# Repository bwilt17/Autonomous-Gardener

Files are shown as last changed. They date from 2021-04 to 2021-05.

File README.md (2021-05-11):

# Autonomous Gardener V1.0

A mechatronics course project designed to autonomously care for a potted plant.

## Project Overview 

This project was designed and produced by Manraj Banghu and Beverly Wilt at San Jose State University in Spring 2021. Because of meeting constraints due to the Covid-19 pandemic, the project was done collaboratively online and two physical prototypes were made for testing, one for each team member.

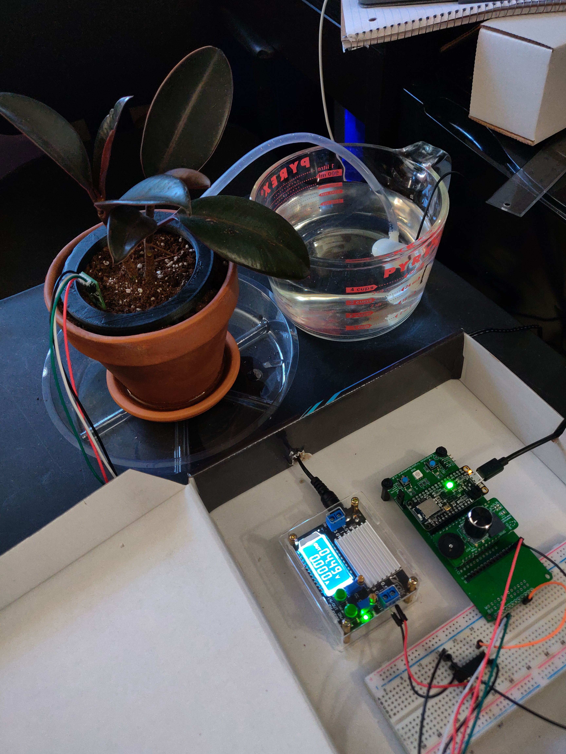
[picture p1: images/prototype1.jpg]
  

## General Design and Goals

**Goal Product:**
  - Autonomous plant caretaker that interfaces the Adafruit nRF52840 sense microcontroller with the following:
    - 3V Water Pump
    - BH1750 Light Sensor(s)
    - STEMMA I2C Capacitive Soil Moisture Sensor

***Note:** Due to shipping issues during the Covid-19 pandemic, the light sensors were ultimately replaced with the integrated temperature sensor on the STEMMA due to lack of connector components.*

**Design Goals:**
  - Not to exceed $100 budget (including university provided components)
  - Sized for reasonable desktop use
  - Makes use of 3D printed water distribution part sized for use in a basic 4.5in terracotta pot from Home Depot and saucer
  - No heavier than 5lbs 

***(UPDATE: 5/10/21)** The final prototype accomplished all of the design goals EXCEPT the weight restriction due to the weight of the water reservoir and moistened soil. Final specifications to be added at a later date.*

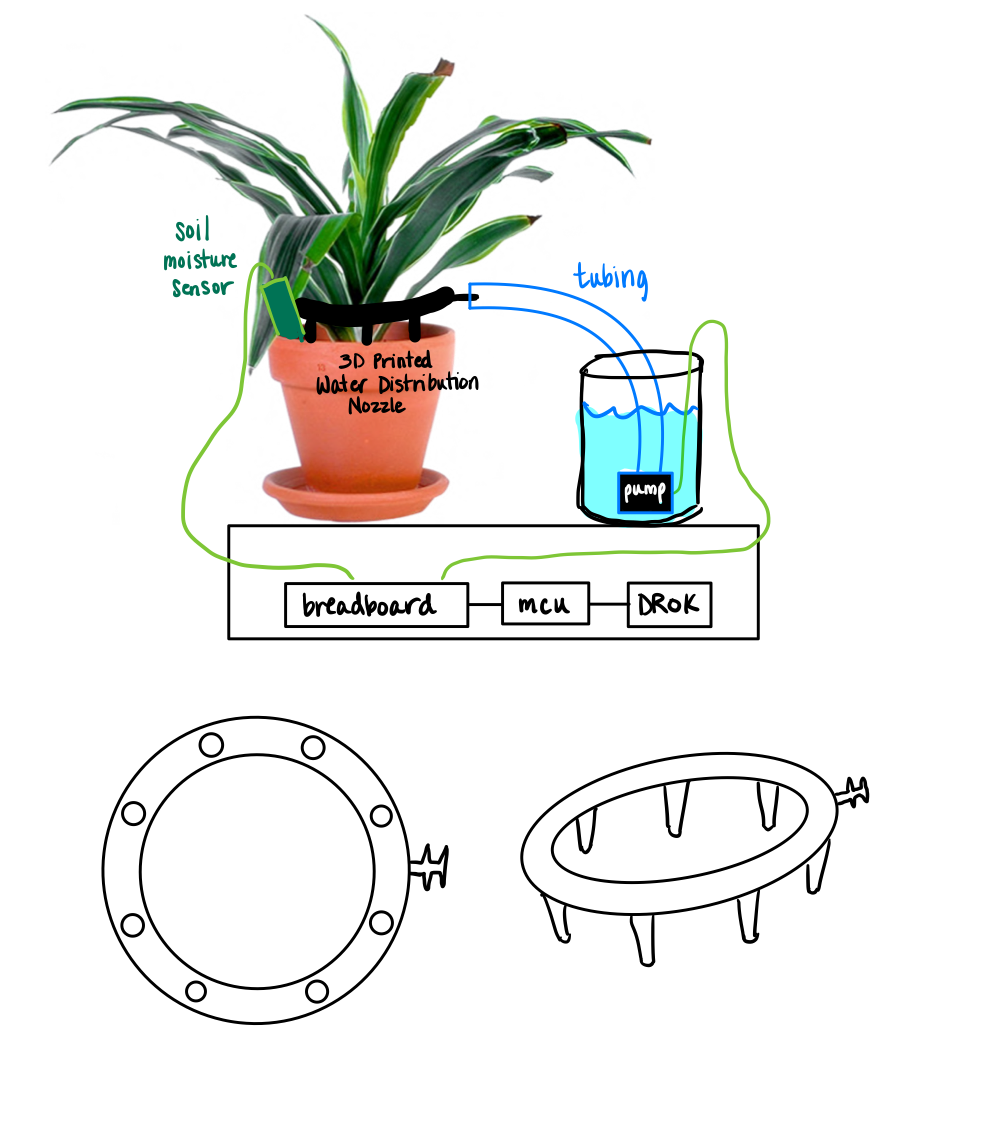
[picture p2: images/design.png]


## Water Distribution Part Info

A part for this project to distribute water around the pot was designed in SolidWorks and 3D printed. Print specifications and 3D model files can be found under [CAD files](https://github.com/bwilt17/Autonomous-Gardener/tree/main/CAD%20files).

***(UPDATE: 4/5/21)** Part design needs to be modified to have longer stakes for better soil penetration OR soil level in final potted plant used must be specified to be no lower than approx. 1/2" from the top edge of the pot.*

***(UPDATE: 5/10/21)** For the purposes of this course project, soil level in final potted plant was specified and increased to appropriate level. Another issue found in the final prototype is that the nozzle outlets furthest from the inlet have trouble getting water, presumably because the pump does not fill the nozzle completely in its runtime. Need stronger pump to ensure complete fill and/or narrower interior section.* 

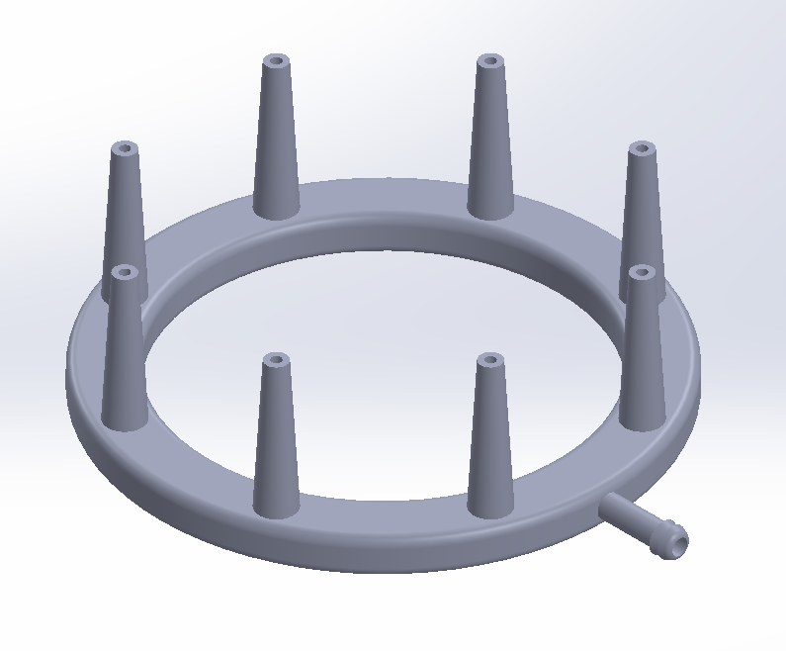
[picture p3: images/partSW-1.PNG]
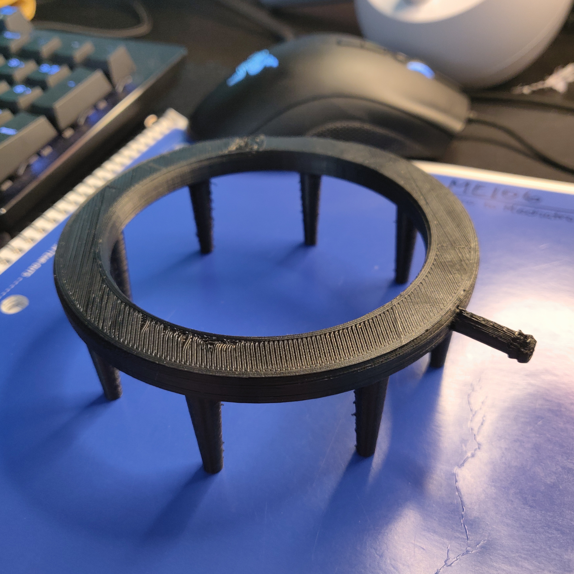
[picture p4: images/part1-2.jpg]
 

## Circuit Design:

The interface circuit makes use of a darlington transistor acting as a switch for the pump control. This simplified the circuit design, as it was similar to a setup from a course lab assignment, and allowed us to PWM for better control over pump speed. 

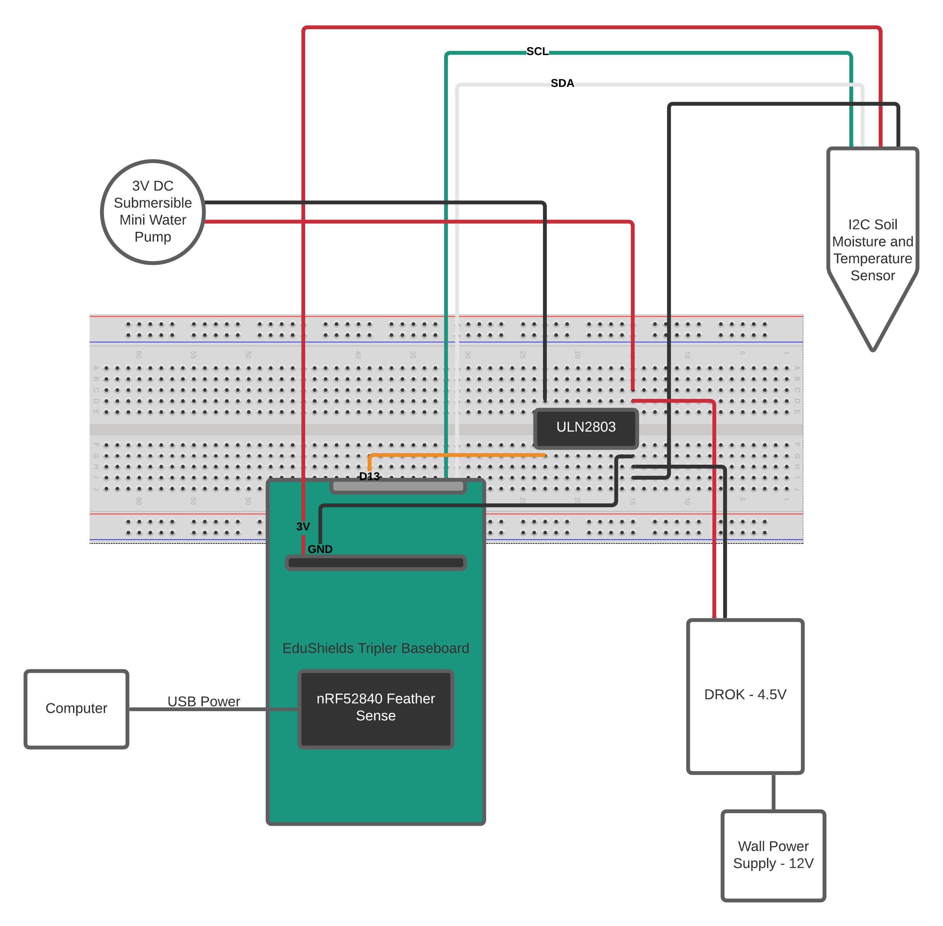
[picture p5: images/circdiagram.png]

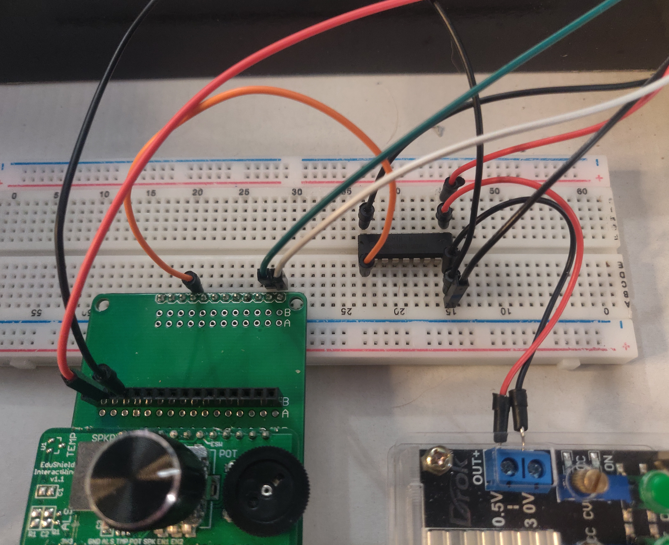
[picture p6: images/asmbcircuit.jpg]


## Coding

The program for the autonomous gardener was made in CircuitPython with Mu as a main editor and user interface. The full code, as presented for the course, can be found under [code](https://github.com/bwilt17/Autonomous-Gardener/tree/main/code).

A general flowchart for the program can be seen below:

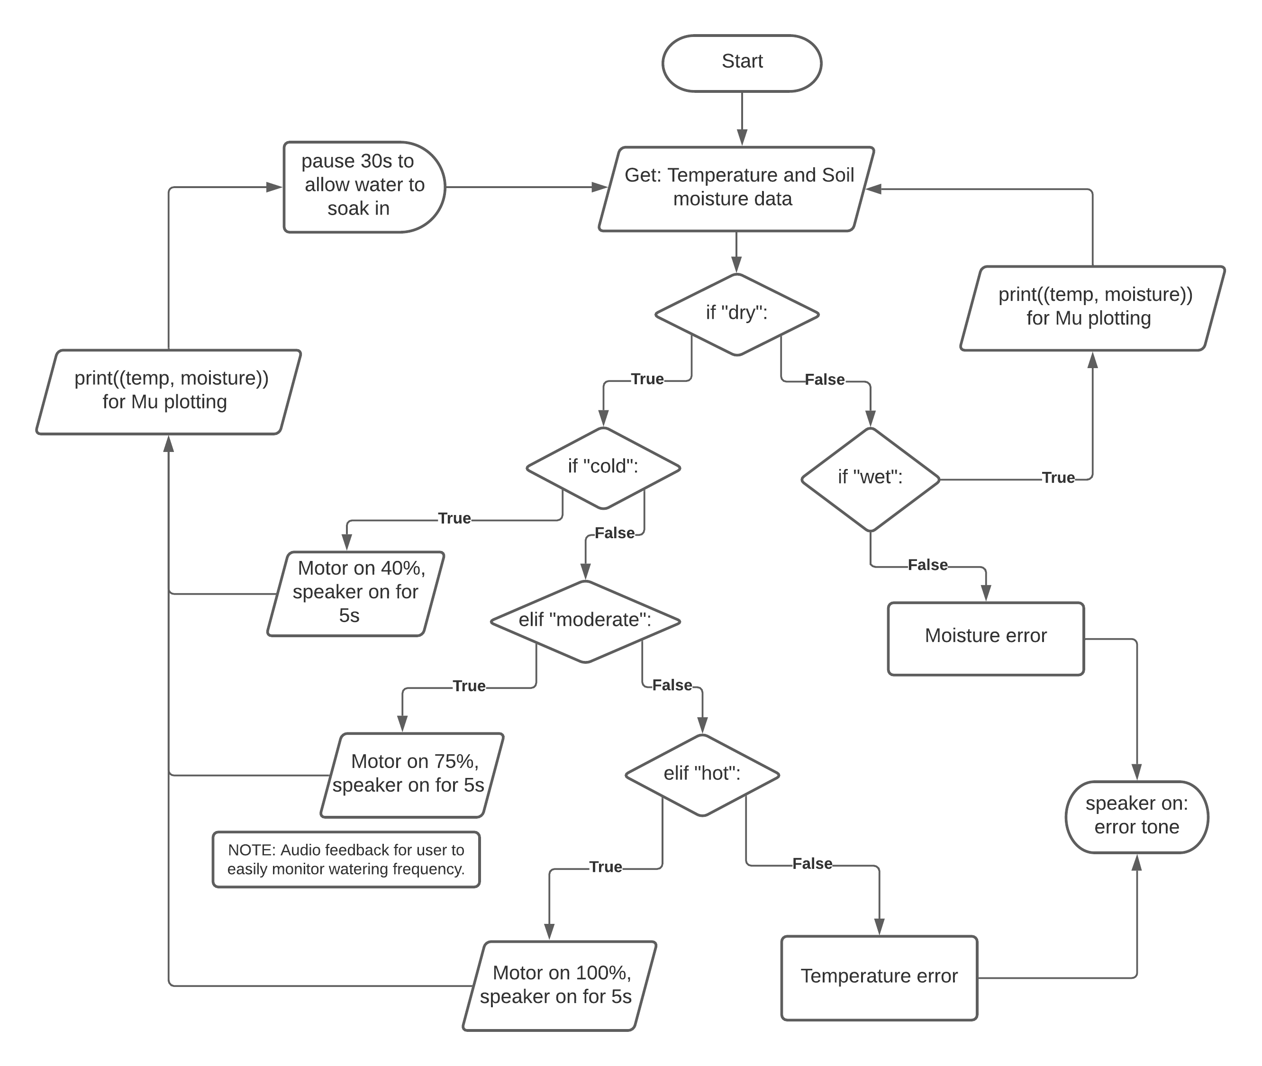
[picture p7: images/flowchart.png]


## Proof of Functionality

A short video showcasing the prototype's functionality can be found on [Youtube](https://www.youtube.com/watch?v=F2NkZJcwzsY).

## Improvements/Recommendations

The following are some suggestions for future improvement, to be done in V2.0: 
  - Decrease electronics footprint by putting nRF directly on breadboard 
     - Need external speaker OR replace moisture sensor with one that has integrated speaker to keep error/pump audio cues
  - Waterproof box to contain electronics to prevent shorting/damage
  - Add a water level sensor (ultrasonic sensor?) to the reservoir to prevent motor damage due to low water level
  - Battery/LCD screen integration to remove need for computer tether
  - Larger water reservoir for less user-dependency
  - Housing that combines electronics, reservoir, etc. into a more polished product
  - Different plant type scenarios (ie. succulent, tropical, etc.) for moisture regulation, or allow for user input

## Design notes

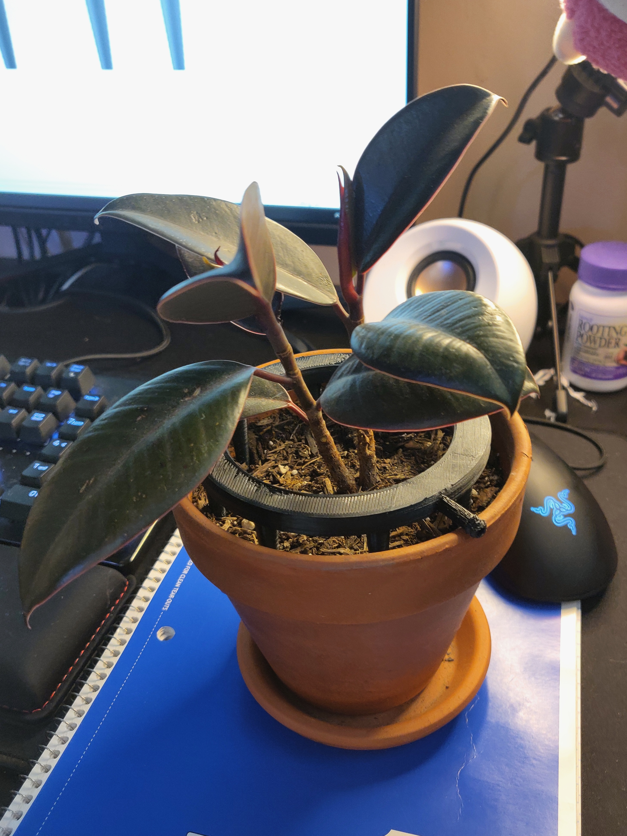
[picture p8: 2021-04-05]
images/part1-1.jpg

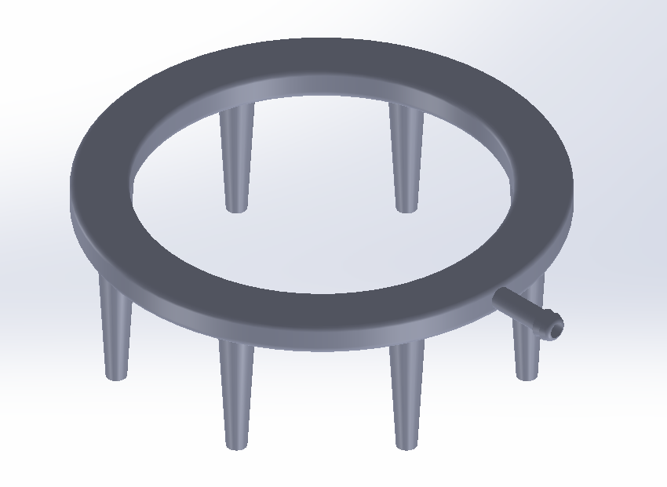
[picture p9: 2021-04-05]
images/partSW-2.PNG

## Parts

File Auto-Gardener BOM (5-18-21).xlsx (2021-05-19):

Index | Quantity | Description | Product Link (NOTE: Adafruit components also available from Digi-Key by searching product number) | Unit Price (USD) | Extended Price (USD)
1 | 1 | TUBING PVC 6MM ID X 1 METER | https://www.adafruit.com/product/4545 | $1.50 | $1.50
2 | 1 | SUBMERSIBLE 3VDC HORIZONTAL PUMP | https://www.adafruit.com/product/4546 | $1.95 | $1.95
3 | 1 | ADAFRUIT STEMMA SOIL SENSOR | https://www.adafruit.com/product/4026 | $7.50 | $7.50
4 | 3 | ADAFRUIT BH1750 LIGHT SENSOR | https://www.adafruit.com/product/4681 | $4.50 | $13.50 | NOT USED
5 | 1 | ADAFRUIT NRF52840 FEATHER SENSE WITH BASEBOARD AND INTERACT WING | Provided by SJSU, components available from Adafruit. (see below) | $40.00 | $40.00
6 |  |  | https://www.adafruit.com/product/4516
7 | 2 | STEMMA QWIIC JST SH CABLE 100MM | https://www.adafruit.com/product/4210 | $0.95 | $1.90 | NOT USED
8 | 1 | JST SH 4-PIN TO PREMIUM MALE HEADER | https://www.adafruit.com/product/4209 | $0.95 | $0.95 | NOT USED
9 | 1 | JST PH 4-PIN TO MALE HEADER CABLE | https://www.adafruit.com/product/3955 | $1.50 | $1.50
10 | 1 | FULL-SIZE SOLDERLESS BREADBOARD | https://www.adafruit.com/product/239 | $5.95 | $5.95
11 | 1 | JUMPER WIRE M TO F 6" 28AWG | https://www.adafruit.com/product/1954 | $1.95 | $1.95
12 | 1 | JUMPER WIRE M TO M 6" 28AWG | https://www.adafruit.com/product/1957 | $3.95 | $3.95
13 | 1 | PENNINGTON 4.5'' TERRA COTTA CLAY POT | https://www.homedepot.com/p/Pennington-4-5-in-Terra-Cotta-Clay-Pot-100043011/100332408 | $0.97 | $0.97
14 | 1 | PENNINGTON 4.25'' TERRA COTTA CLAY SAUCER | https://www.homedepot.com/p/Pennington-4-25-in-Terra-Cotta-Clay-Saucer-100043034/100175939 | $0.97 | $0.97
 |  | NOTE: Cost of 3D printing filament not included, considered to be negligible as it would be an unknown fraction of the price of a spool.
 |  | For reference, a 1kg spool of PLA filament is generally $20-25.
 |  |  |  | Total Cost (USD): | $66.24 | (Does not included unused components)
 |  |  |  | (not including tax/shipping)
 |  |  |  | Budget (USD): | $100.00
 |  |  |  | (not including tax/shipping)
 |  |  |  | Difference (USD): | $33.76

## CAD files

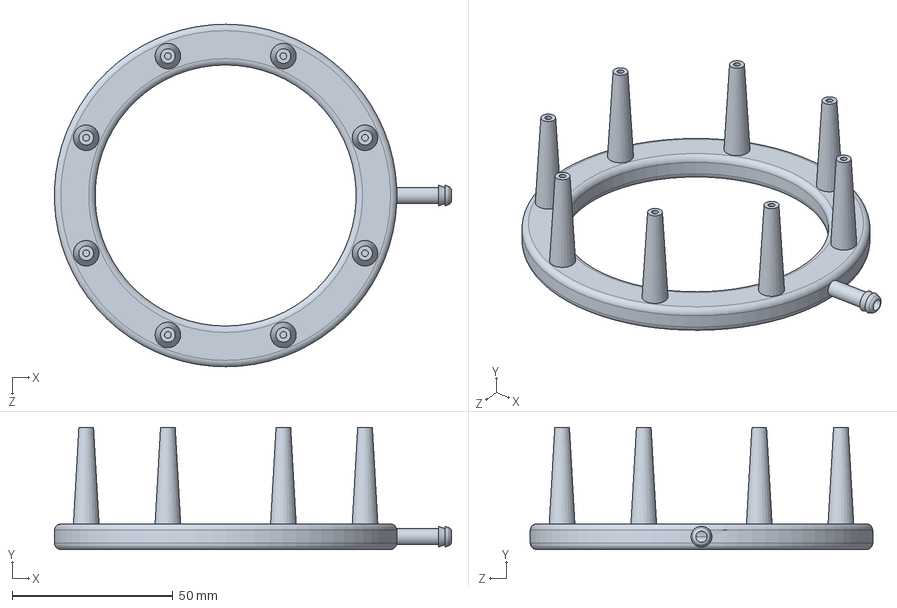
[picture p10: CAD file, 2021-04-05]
CAD files/waterpart.SLDPRT
123.6 x 38.0 x 106.7 mm

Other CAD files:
CAD files/waterpart.STL

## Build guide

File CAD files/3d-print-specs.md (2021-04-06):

# 3D Print Specifications

Printer: Kingroon KP3

Filament Type: PLA 

Filament Brand: Hatchbox

Nozzle Temp: 190 C

Bed Temp: 60 C

Printing Speed: 30 mm/s

Supports?: Yes

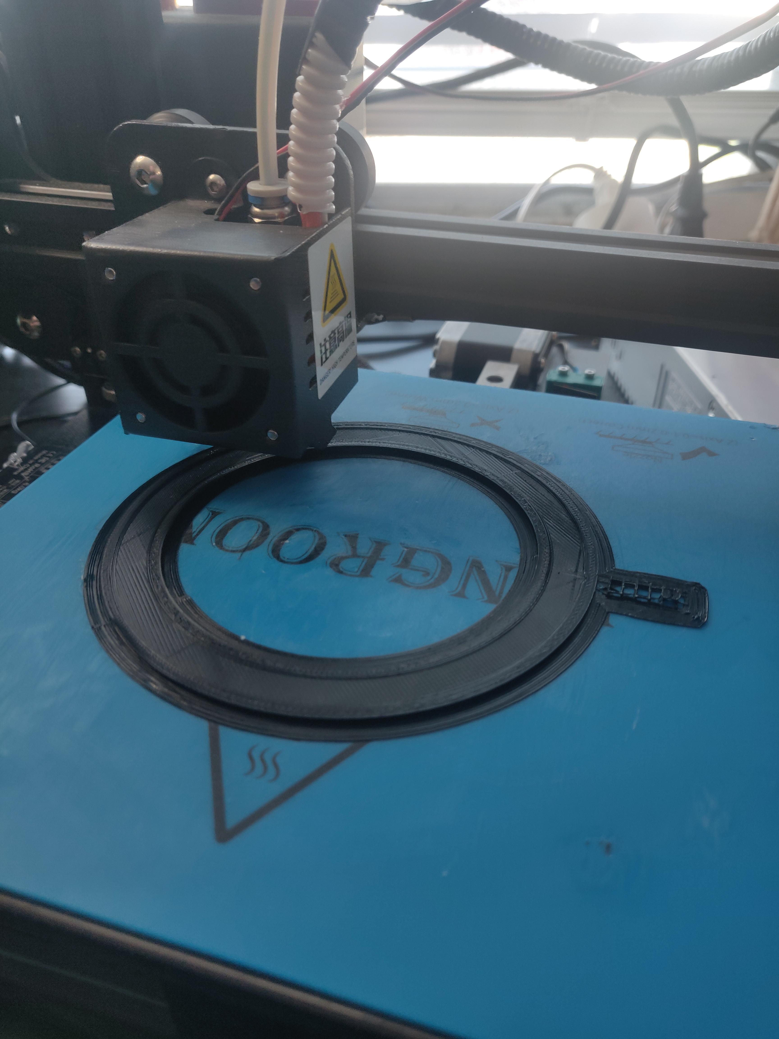
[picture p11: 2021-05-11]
images/print.jpg

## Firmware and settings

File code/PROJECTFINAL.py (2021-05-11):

import board
import pulseio
import time
from board import SCL, SDA
import busio
from adafruit_seesaw.seesaw import Seesaw

motor = pulseio.PWMOut(board.D13)
i2c_bus = busio.I2C(SCL, SDA)
ss = Seesaw(i2c_bus, addr=0x36)
spkr_pwm = pulseio.PWMOut(board.A3, variable_frequency=True)

frequency = 659

lastTime = time.monotonic()

def pwm_level(pin, inc):
    pin.duty_cycle = int((0.1 * inc) * ((2 ** 16) - 1) - 0.1)

def play(freq):
    spkr_pwm.frequency = freq
    spkr_pwm.duty_cycle = 2 ** 15

def stop():
    spkr_pwm.duty_cycle = 0

def error_beep():
    while True:
        play(650)
        time.sleep(1)
        play(450)
        time.sleep(1)
        play(250)

def readingsensor(SoilVal, TempVal, last_time):
    if SoilVal <= 400:  # Get data from soil sensor dry
        if TempVal <= 0:
            print("Weather is too cold! Bring plant to warmer area.")
            error_beep()
        elif 0 < TempVal <= 13:  # cold data from temp
            print("The plant is dry and the temperature is cold.")
            print("-> Pump on")
            play(frequency)  # Play speaker
            motor.duty_cycle = int(0.4*(2**16-1))
            time.sleep(5)
            motor.duty_cycle = 0
            stop()
        elif 13 < TempVal <= 28:  # moderate data from temp
            print("The plant is dry and the temperature is moderate.")
            print("-> Pump on")
            play(frequency)  # Play speaker
            motor.duty_cycle = int(0.75*(2**16-1))
            time.sleep(5)
            motor.duty_cycle = 0
            stop()
        elif 28 < TempVal <= 36:  # hot data from temp
            print("The plant is dry and the temperature is hot.")
            print("-> Pump on")
            play(frequency)  # Play speaker
            motor.duty_cycle = (2**16-1)
            time.sleep(5)
            motor.duty_cycle = 0
            stop()
        elif 36 < TempVal:  # extreme data from temp
            print("Weather is too hot! Bring plant to cooler area.")
            error_beep()
        else:
            print("Temperature error. Please check sensor.")
            error_beep()
    elif 400 < SoilVal <= 1000:  # Get data from soil sensor (wet)
        print("Soil is already moist and does not need to be watered.")
    elif SoilVal > 1000:
        print("Overwatered! Please check plant.")
        error_beep()
    else:
        print("Soil Moisture error. Please check sensor.")
        error_beep()

def plot(s,t):        # Plot the data print((moisture, temp))
    print((s, t))
    time.sleep(0.5)

while True:
    # Read sensor
    SoilVal = ss.moisture_read()
    TempVal = ss.get_temp()
    plot(SoilVal, TempVal)
    if time.monotonic()-lastTime >= 30:
        lastTime = time.monotonic()
        readingsensor(SoilVal, TempVal, lastTime)

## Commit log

2021-04-05 BOM as of 4/5/2021
    [Auto-Gardener BOM (IN PROGRESS).xlsx]
2021-04-06 Create 3d-print-specs
2021-04-06 Update and rename 3d-print-specs to 3d-print-specs.md
2021-04-06 BOM Update 4/6/21
    [Auto-Gardener BOM (IN PROGRESS).xlsx]
2021-05-11 Update README.md
    Added project descriptions for General Design, Goals, Circuit Design, Coding, Proof of Functionality, and Recommendations
2021-05-19 Updated BOM
    [Auto-Gardener BOM (5-18-21).xlsx]
